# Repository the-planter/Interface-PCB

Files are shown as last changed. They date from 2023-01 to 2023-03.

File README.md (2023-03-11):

# Planter Interface PCB

Interface PCB for an automated hydroponics system, created using KiCad 6.0. 

This PCB enables control and interfacing a Raspberry with several liquid level sensors, 12V peristaltic pumps, a few temperature sensors, and remote controllable outlets.

This PCB acts as a carrier board for various off-the-shelf breakout boards. It enables noise-free signals, painless testing, and robust interfacing of the liquid level sensors, peristaltic pumps, air & water temperature sensors, and electrical outlets. Standardized connector types are used to guarantee secure connections; connector types are differentiated by their purpose and voltage level, to ensure no mismatch between components and voltage levels occur. The use of breakout boards alleviates the difficulties in procuring discrete Integrated Circuits (ICs) during the ongoing chip shortage. 

## Manufactured board
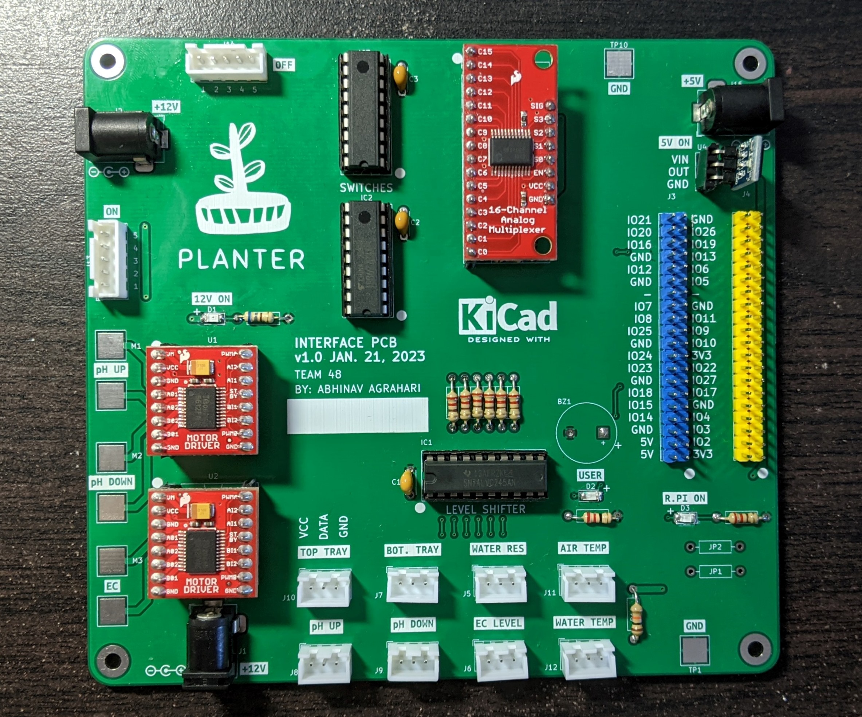
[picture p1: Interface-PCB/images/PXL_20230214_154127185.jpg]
Assembled PCB

| Left View | Right View |
| :---: | :---: |
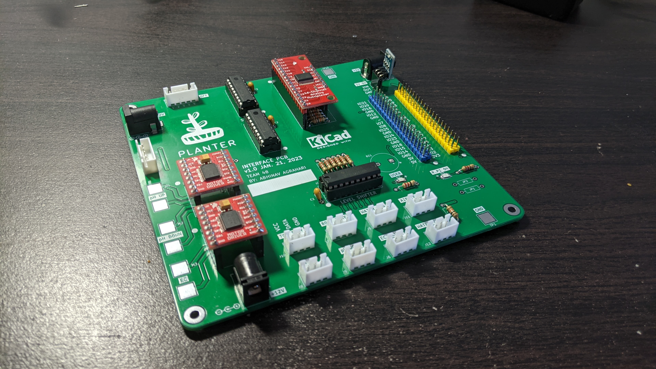
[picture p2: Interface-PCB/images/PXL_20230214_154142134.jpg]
Assembled PCB - Angled left
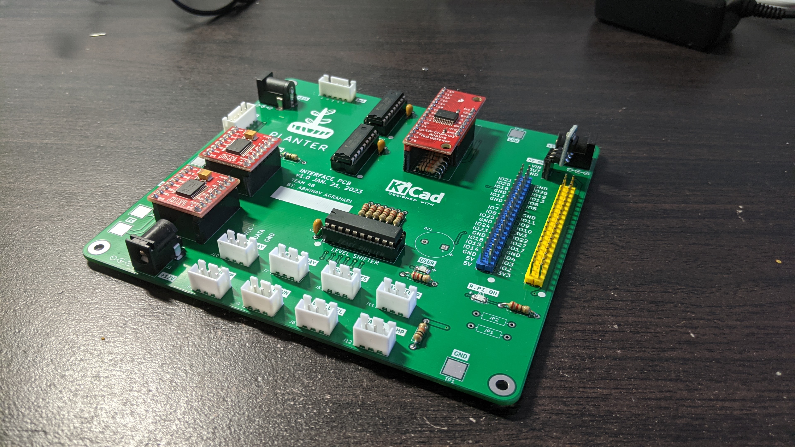
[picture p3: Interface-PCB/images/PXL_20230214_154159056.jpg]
Assembled PCB - Angled right
|  |  |

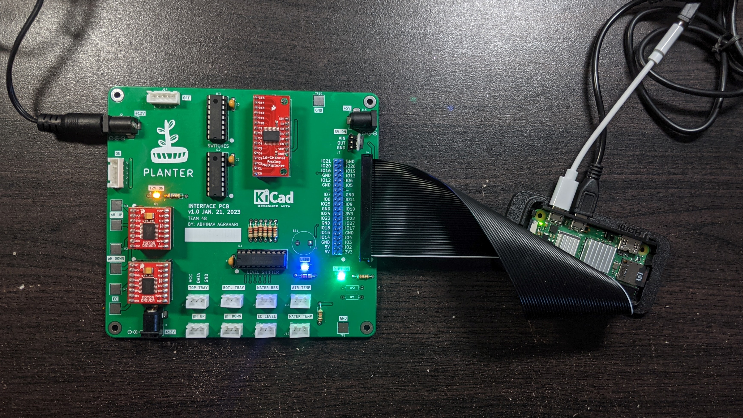
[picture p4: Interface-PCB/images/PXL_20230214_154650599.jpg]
PCB Blinky LED Test


Hooked up to all sensors:

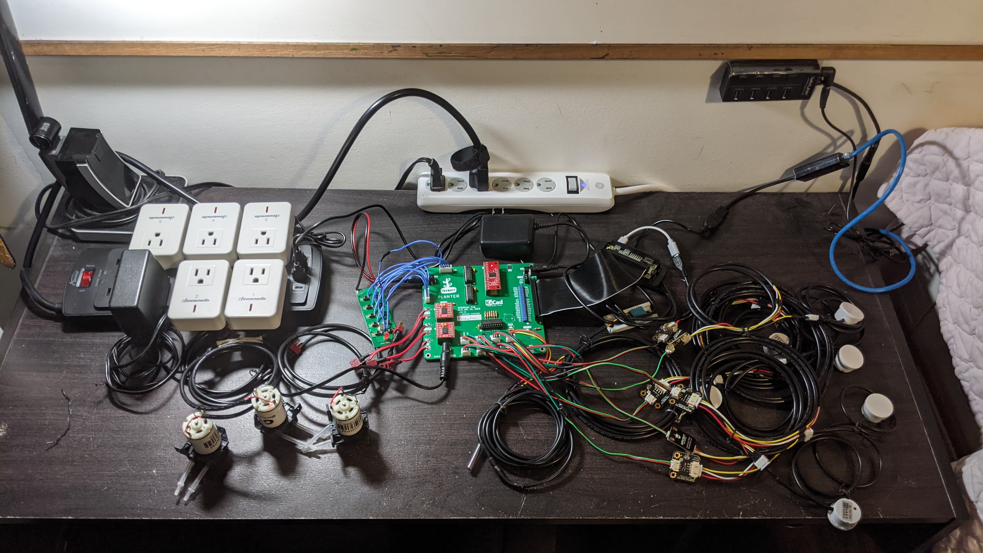
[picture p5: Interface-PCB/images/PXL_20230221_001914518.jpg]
All Electronics connected

## Renders
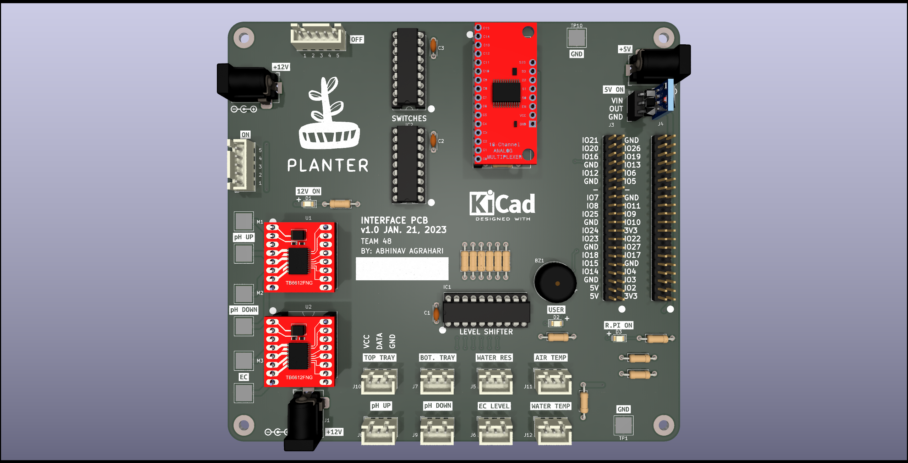
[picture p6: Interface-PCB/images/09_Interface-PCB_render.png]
PCB Render


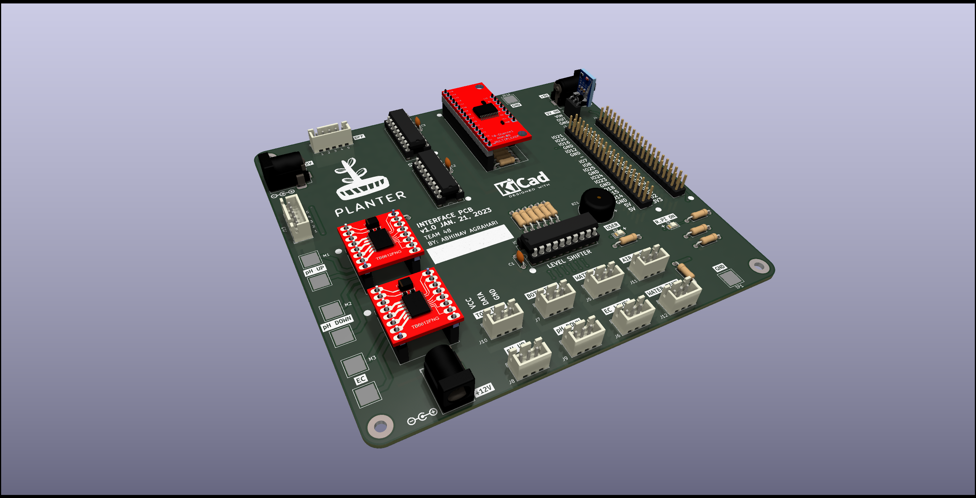
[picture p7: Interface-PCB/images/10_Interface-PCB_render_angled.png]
PCB Render angled

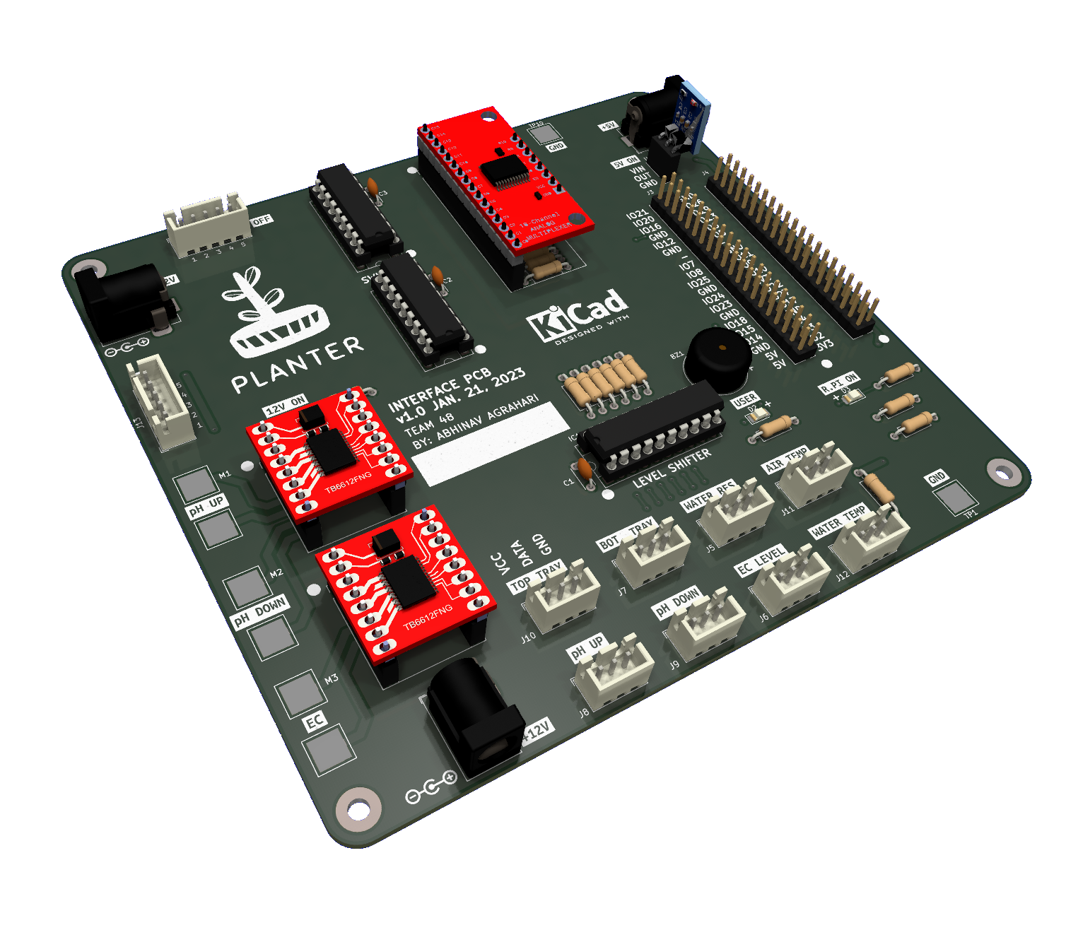
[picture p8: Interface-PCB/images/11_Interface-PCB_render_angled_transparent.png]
PCB Render angled


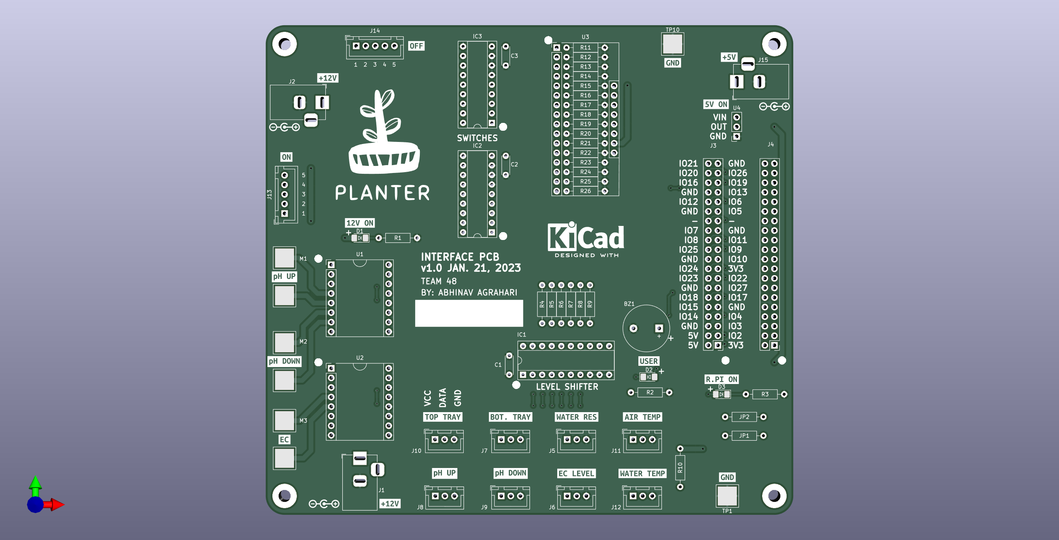
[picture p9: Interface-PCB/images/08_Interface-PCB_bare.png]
PCB Bare


## Routing
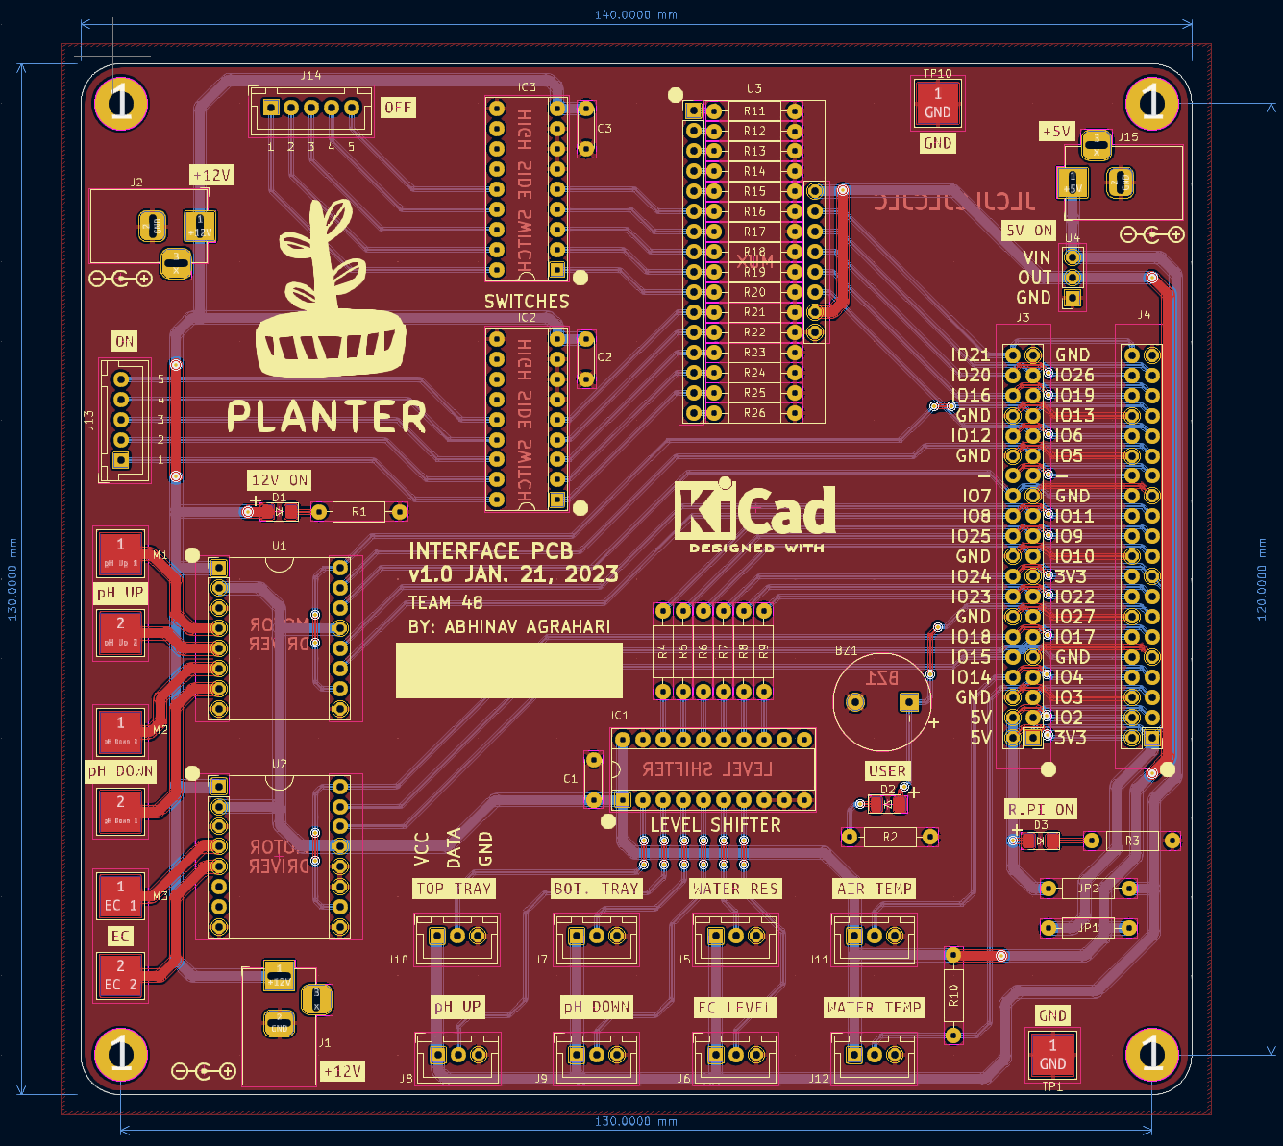
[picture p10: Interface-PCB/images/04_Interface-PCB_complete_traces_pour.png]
PCB Traces with Pour


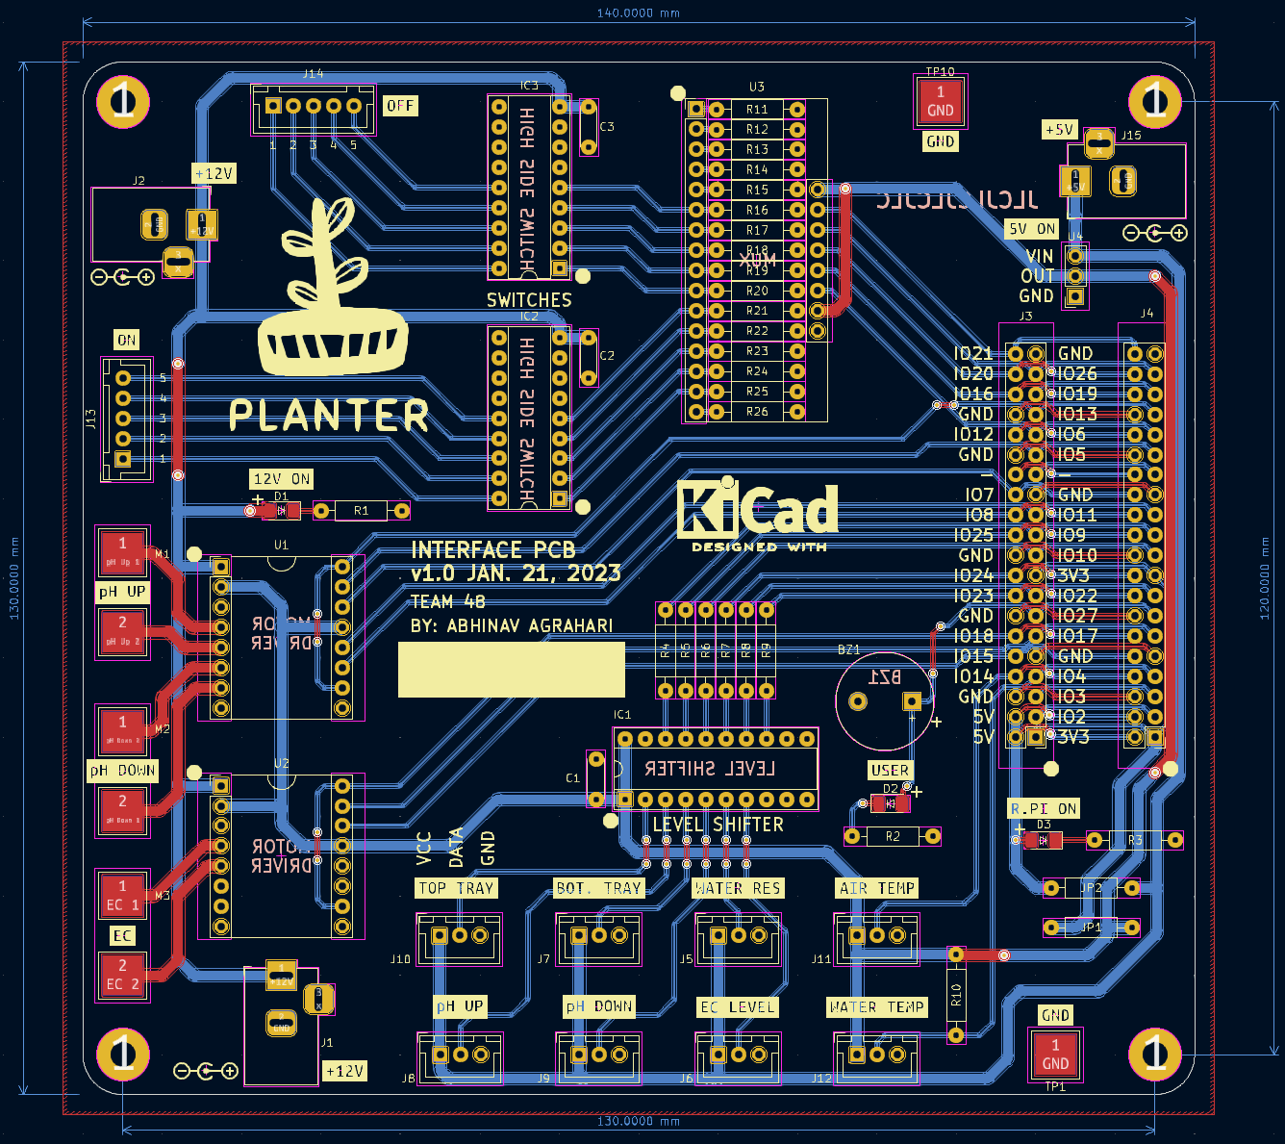
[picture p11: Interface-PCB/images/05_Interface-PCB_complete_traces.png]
PCB Traces


## Mechanical Team's Enclosure
The PCB is placed in the top shelf of the enclosure designed by the Mechanical Team
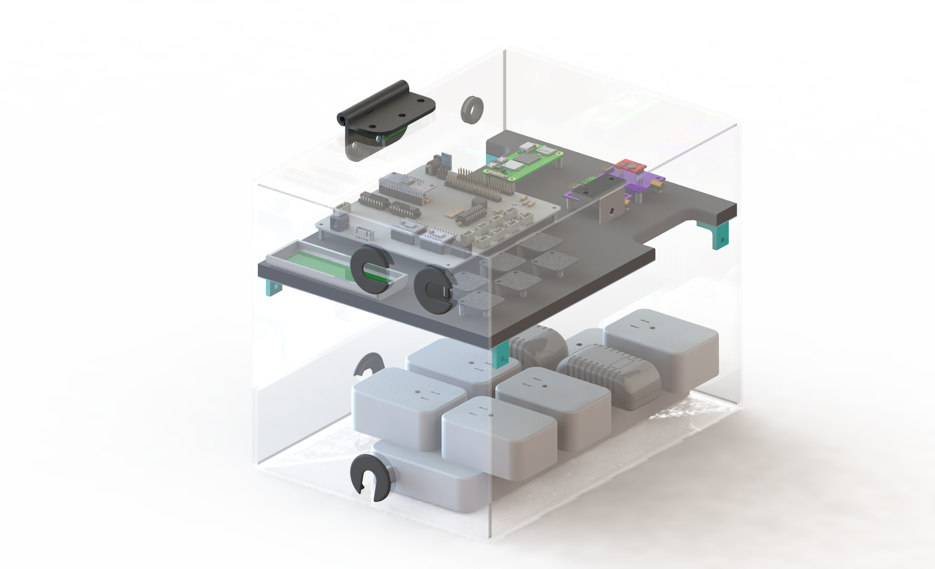
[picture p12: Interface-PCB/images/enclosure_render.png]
PCB in Enclosure - Rendered


## Schematic

Main Schematic
Sensors Schematic
Power Schematic
Remote Control Outlets Schematic

## Repo Setup
- Setup KiCad 6.0 using my [kicad-libraries](https://github.com/AbhinavA10/kicad-libraries)

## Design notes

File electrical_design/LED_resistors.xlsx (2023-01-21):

Purpose | Supply Voltage | LED Type | LED Color | FWD Voltage | FWD Current mA | FWD Current mA Designed | Calculated R Value | Closest 5% | Actual Current mA | R Power
Indicator | 12 | 3mm | RED | 1.85 | 20 | 15 | 676.6666667 | 680 | 14.9 | 0.1515036765
 | 12 | SMD | YELLOW | 1.8 | 20 | 15 | 680 | 680 | 15.0 | 0.153
Indicator | 5 | 3mm | GREEN | 2.1 | 20 | 15 | 193.3333333 | 220 | 13.2 | 0.03822727273
 | 5 | SMD | GREEN | 2.4 | 20 | 15 | 173.3333333 | 220 | 11.8 | 0.03072727273
User LED | 3.3 | 3mm | RED | 1.85 | 20 | 15 | 96.66666667 | 100 | 14.5 | 0.021025
 | 3.3 | SMD | BLUE | 3 | 20 | 15 | 20 | 22 | 13.6 | 0.004090909091

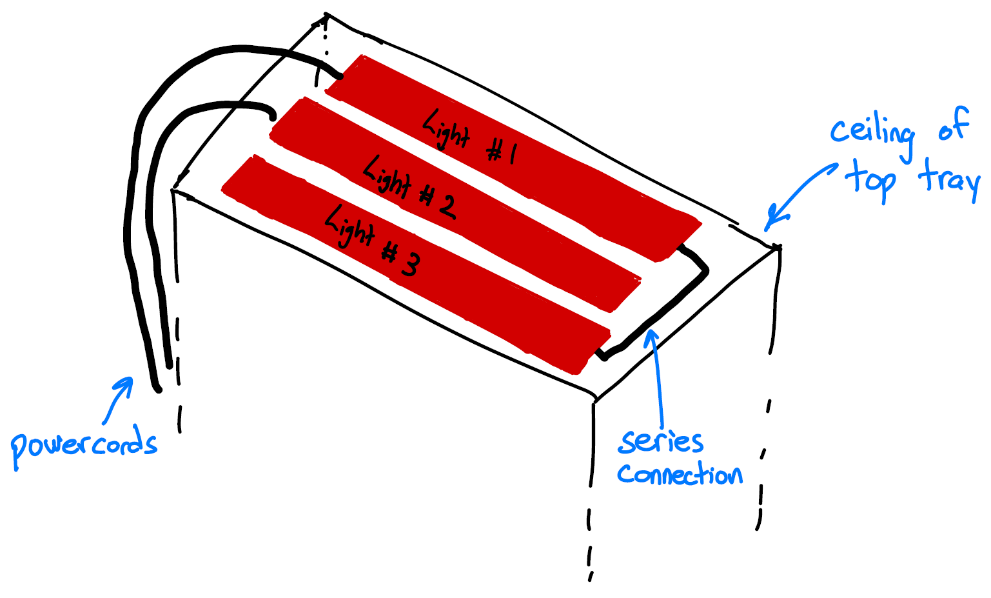
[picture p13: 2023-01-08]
electrical_design/Lights_position.png

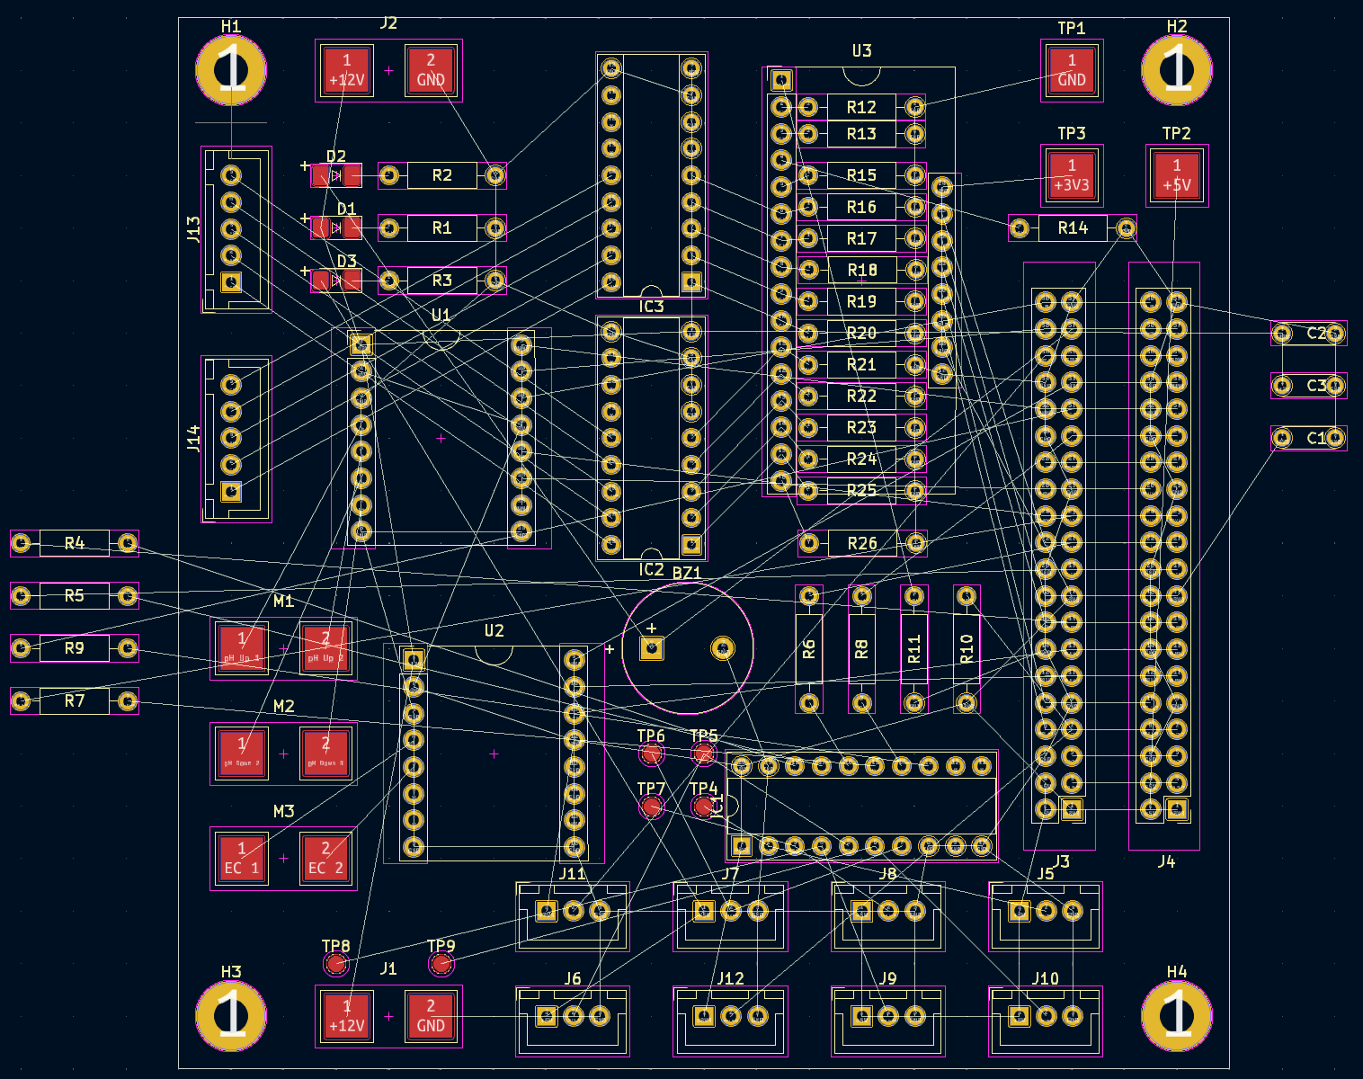
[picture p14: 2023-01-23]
Interface-PCB/images/00_initial_layout.png

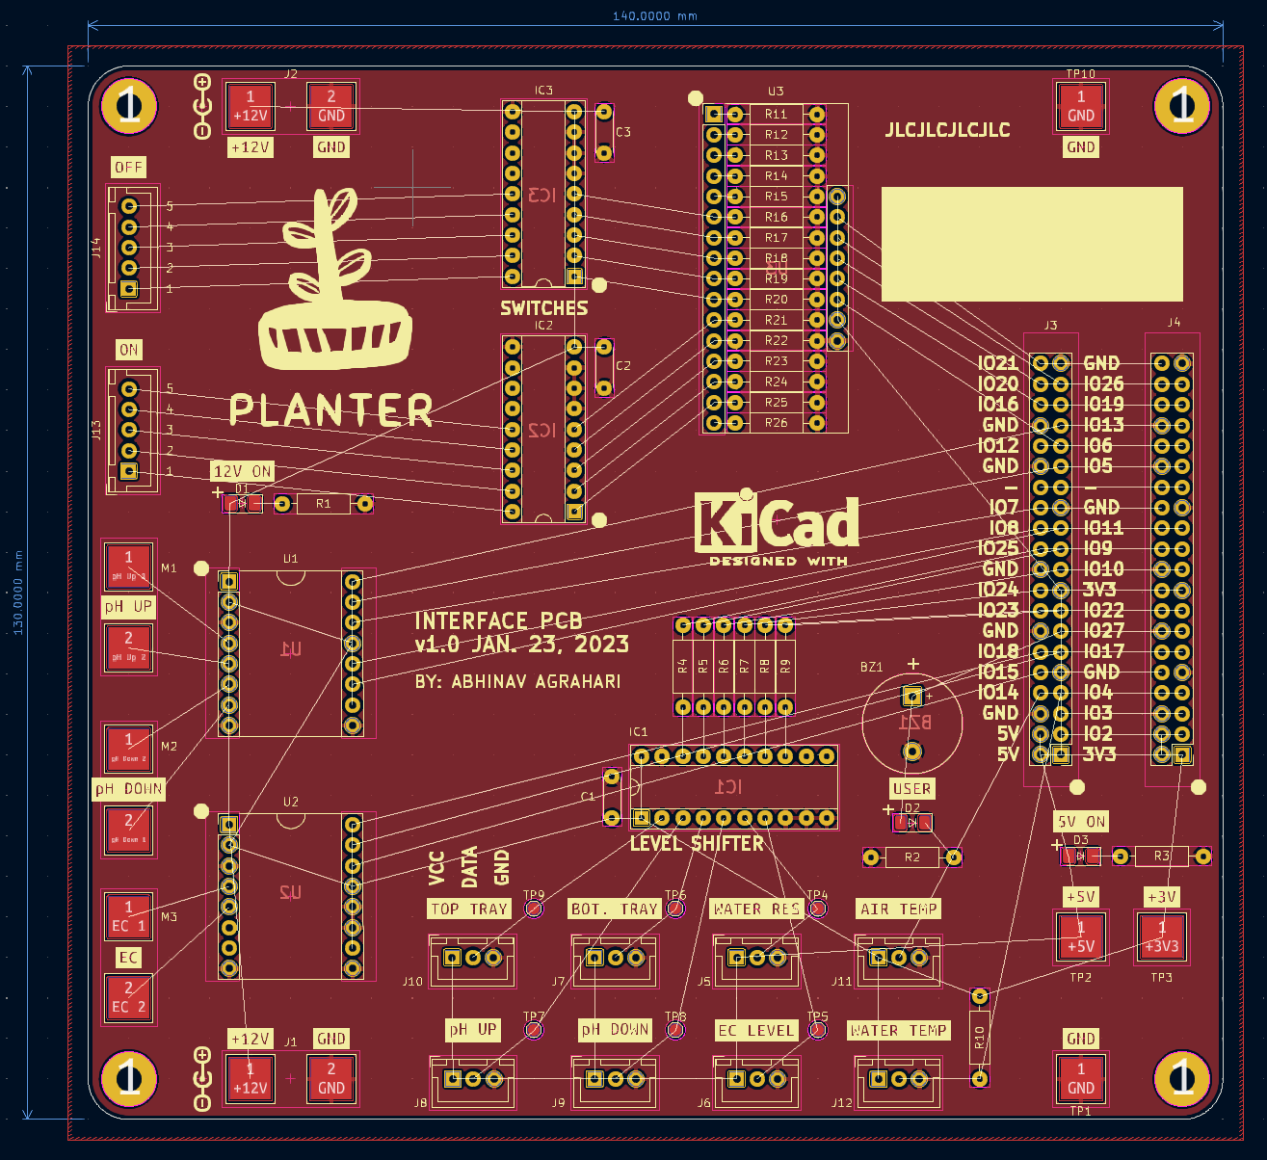
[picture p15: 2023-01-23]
Interface-PCB/images/03_complete_silkscreen.png

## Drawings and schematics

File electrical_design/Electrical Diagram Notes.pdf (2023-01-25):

PCBLayout | Custom PCB
/

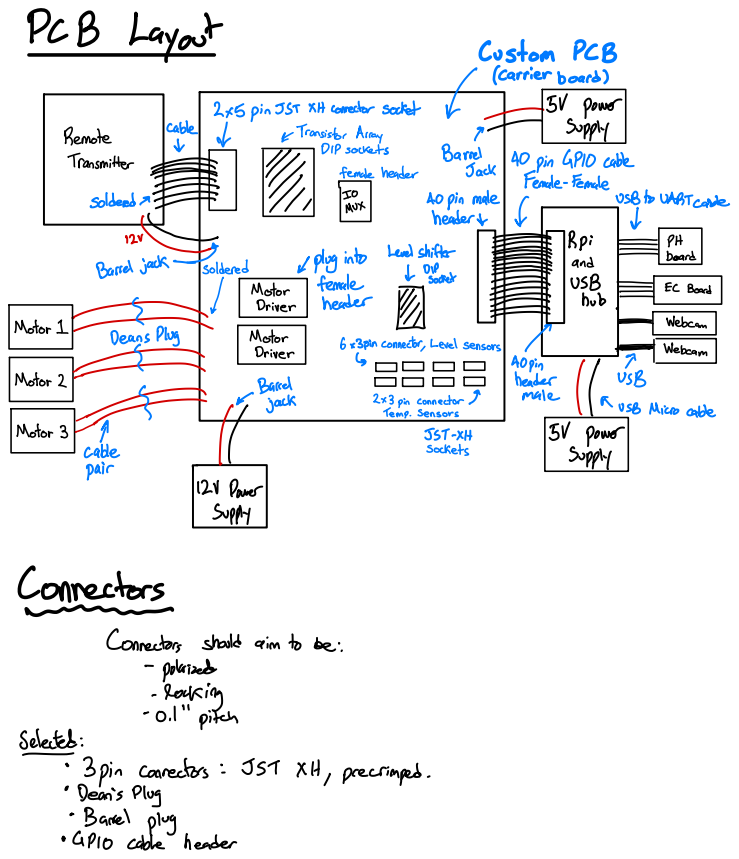
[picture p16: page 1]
(carrier board); 2x5 pin5STXHconnector socket; 50 power; Remote; cable; &Transistor Array; soppl; DIP sockets; Barrel Jack Transmitter -; ↑.'=x 40 pin GP10 cable ->; female header; Female-; Female; soldered a=; 40 pin male; USB toUARTble; header&; Rpi; PHd; Barrel jack &; soldered; Motor; female; ↓Plcket; Eand; Driver; header; nBb =; ICBoard; Motor I-; Webcam; Deans Plug; 6x3pinconnector, Level sensors; Iam; Motor 2; GOPe; Barrel; jack; 2x3 pin connector &; male; 1)aUSB Micro cable --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

↓ plug intoLevel shifter

Connectors should aim tobe:
polarized
·locking -
0.1"pitch

selected3pin connectors:JST XH, precrimped ·

# Baboard Dimensions Pitch -

90.1"

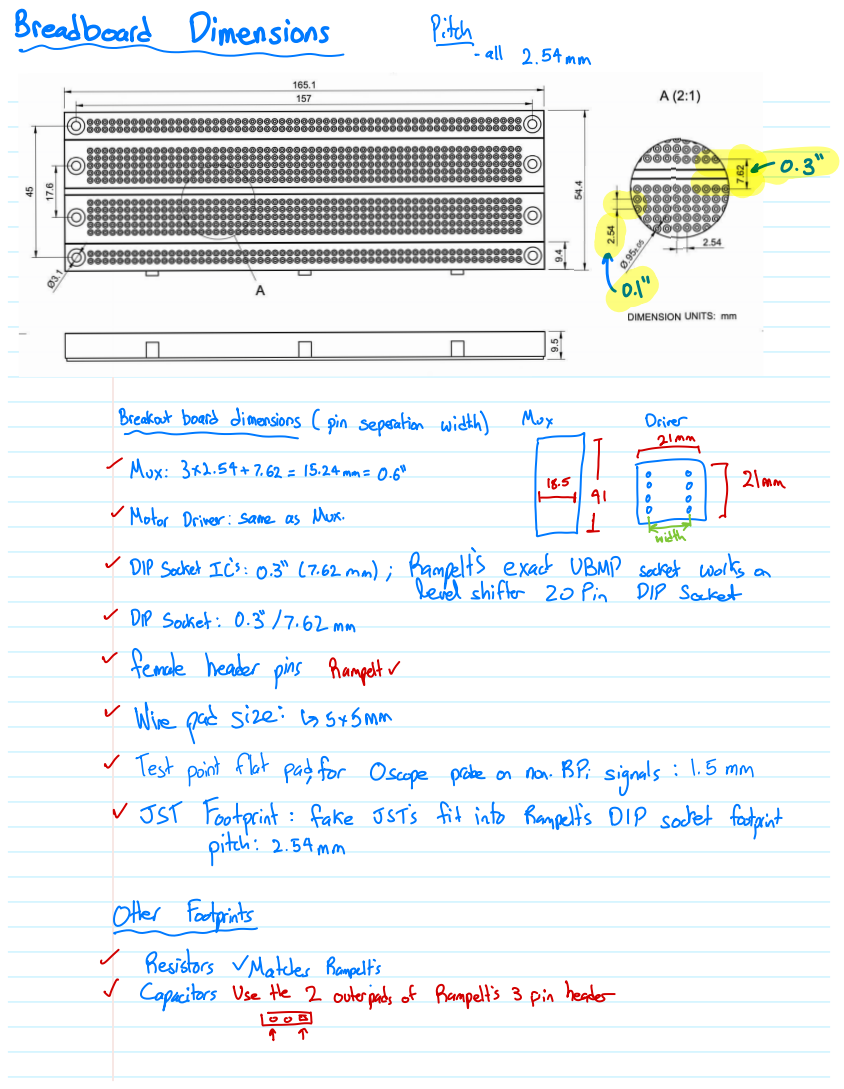
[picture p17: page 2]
all 2.54mm; Breakoutboard dimensions -; (pin separation width); Mox; Driver; Mox:3x2.54+ 7.62 =; Day7:JCl; ~Motor Driversame as; Nux.; kith!; level shifter 20 Pic; DIP socket; ~ Testpointflatpad, for Oscope probe on; non. RPisignals:¹.5 mm; #Footprints; Resistors ~Matches Rampelt's

~ DIP SocketICs:0.3" (.62mm);Rampelt's exactUBMPsocret works or

~ DIPSocket:0.3" /7.62mm
female header pins Rampeltr

~ Wire pad size:25x5mm
~JSTFootprint: fake JST's fitinto Rampelt's DIPsocket footprint
pitch: 2.54mm

v Capacitors Use the 2 outerpads ofRampelt's 3 pin header

# For

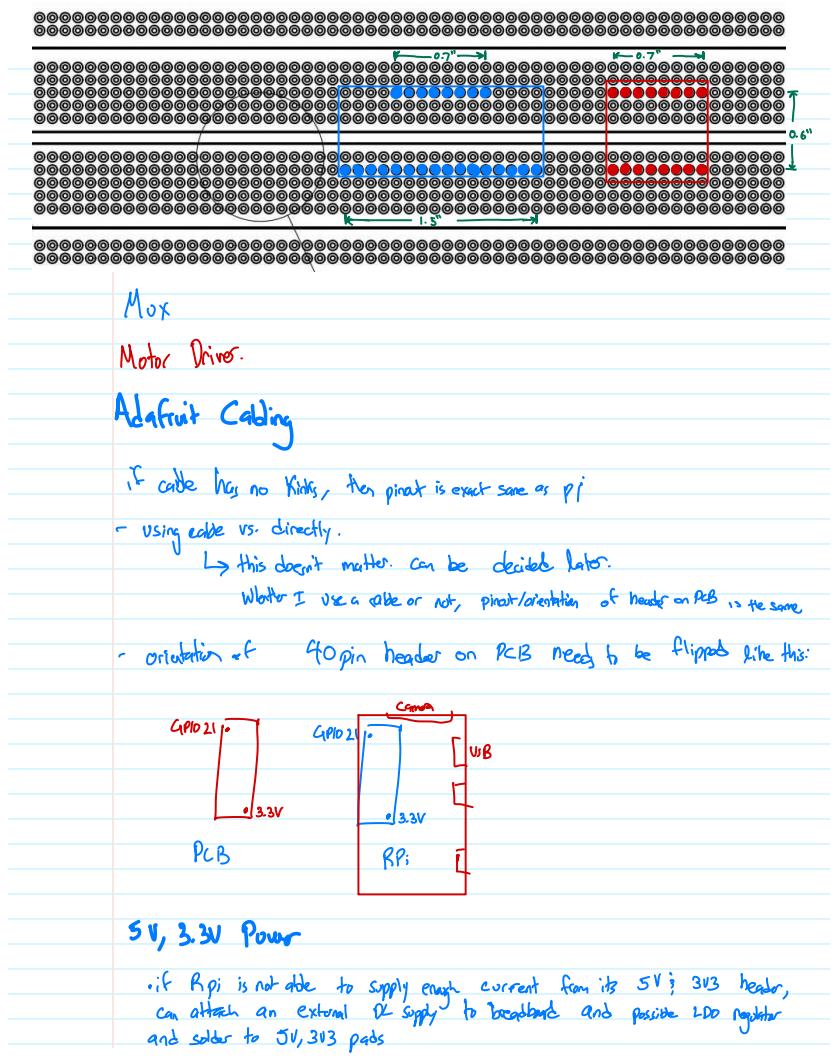
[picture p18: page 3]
Mox; Motor Driver. AdafruitCabling; ifcable has no; kinks, the pinoutis exactsame as; using eable vs. directly.; ↳ this doesn'tmatter. can be; decided later.; Whatter I use a cable or; not, pinotorientation ofheader on PCB is the same; orientation of40pin header on; PCB needs to be; flipped like this:; carea; PCB; can attach an; external; DC supplyto "breadboard and possible CDO regulator and solder to 50,303 pads

5V, 3.30 Power
· ifRpiis notable to supplyenough currentfrom its5V;,303 header,

# Rough BlockDiagrams. Initial Planning

10 NPN transisters | -> | VART

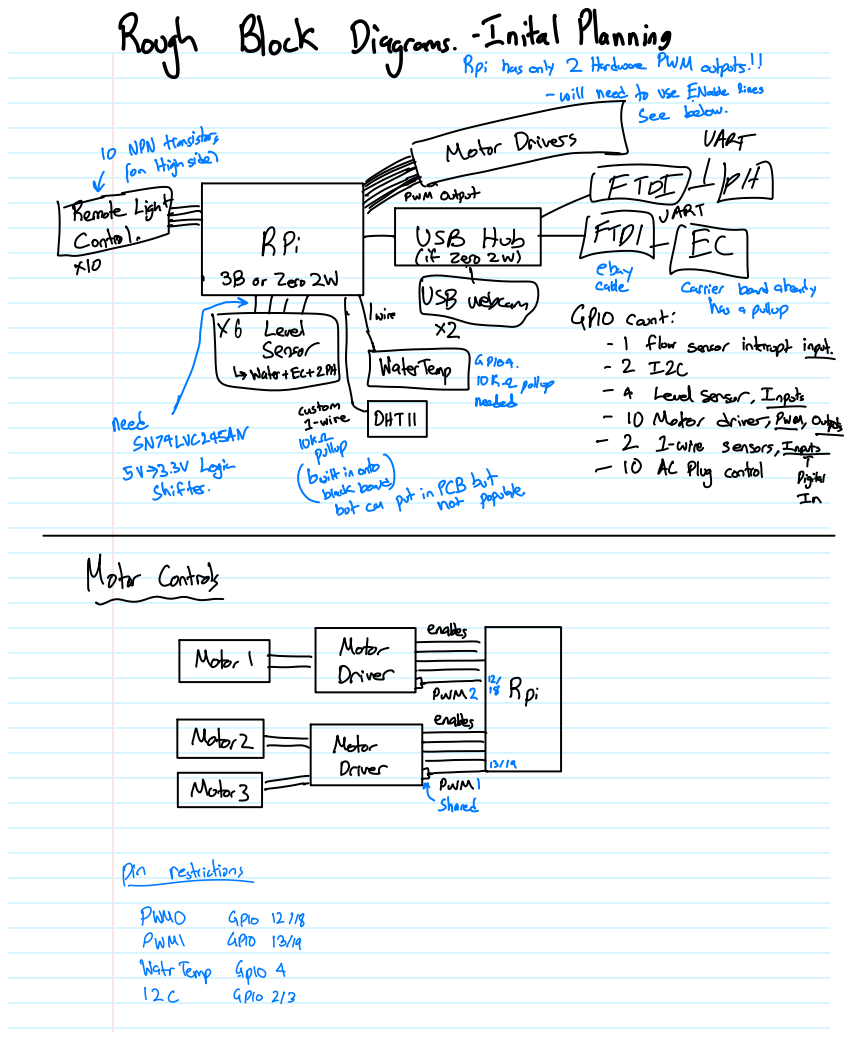
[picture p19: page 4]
see below.; 100 High side); #-puM output; noteLight; ENTERTA; VART; RPi; USB Hub; 3Bor Zero2W; ebay; cable; carrier board already; count:; has a pullup; flow sensor; interruptit. ↑ ⑭ter Tempa P164.; 10kpollo; needed; lead sensor, Inpots; needNT4LVC245AN customre; PHT 1; 10 Motor driver, Iran, opts; 2 I-wire; sensors,Inputs pullup; 5V93.3V Logic; Iwiltin onto&; 10 AC Plug control; Digital shifter.; L blackboard; putinPCB boopulate.; butcal; ↑Controls; enables; MotoI; Motor⁻; PNM2; BRpi; nables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

Rpihas only2 Hardware PWM outpots!!
x2 #sectio reson ano

will need touse Nable lines

Remote Control torequirementsfrom testing.

## 44mAon button

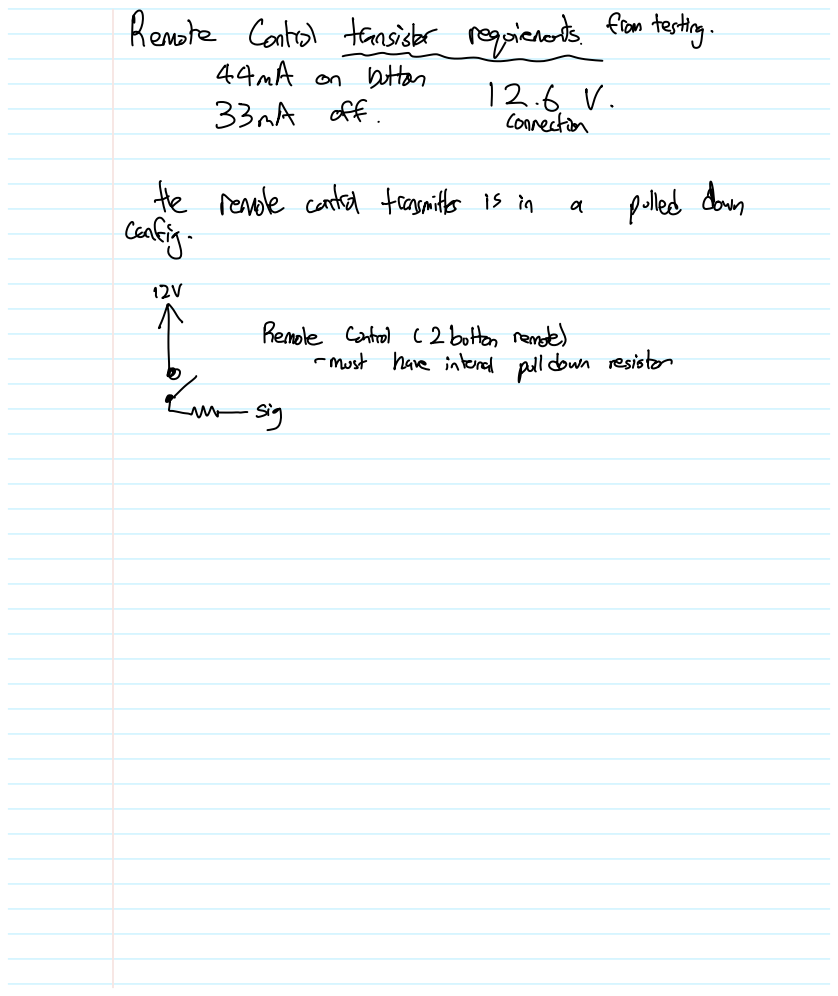
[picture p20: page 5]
33mAoff.; connection; the remote control transmitter is in; polled down; config.; ! Remote Control; (2button remote)

musthave internal pull down resistor
sig

# Routine Blockage norigged

# clogged

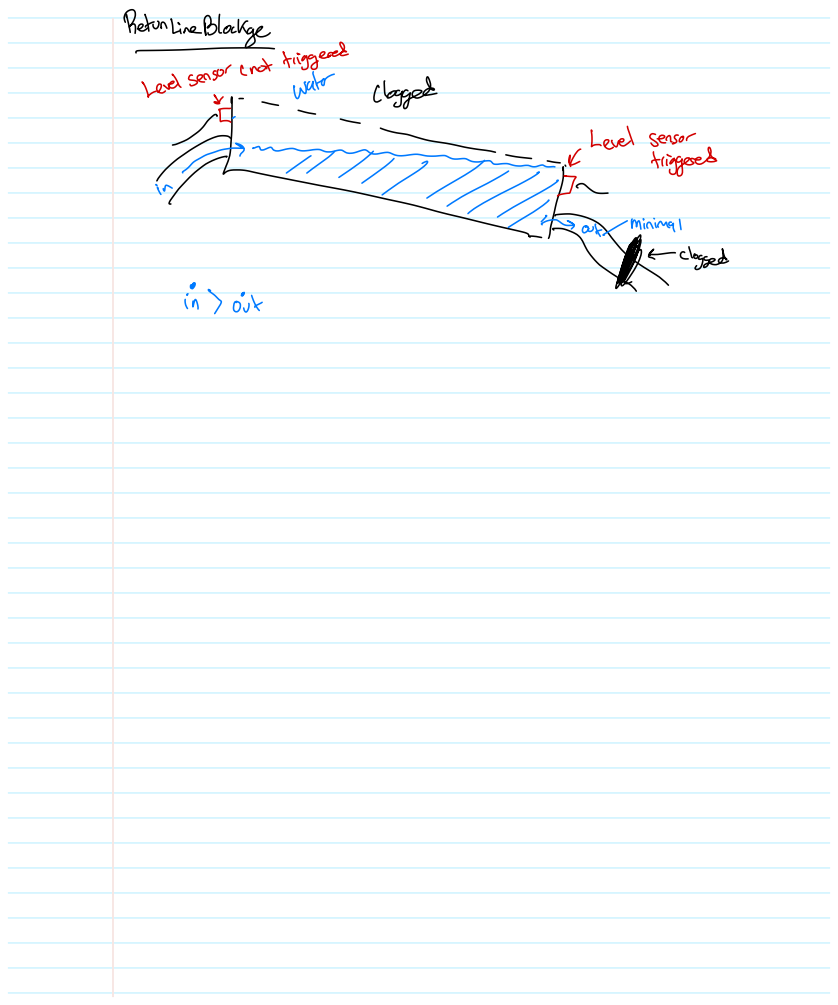
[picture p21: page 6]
Level sensor; triggered i; clogged

# Top

## try

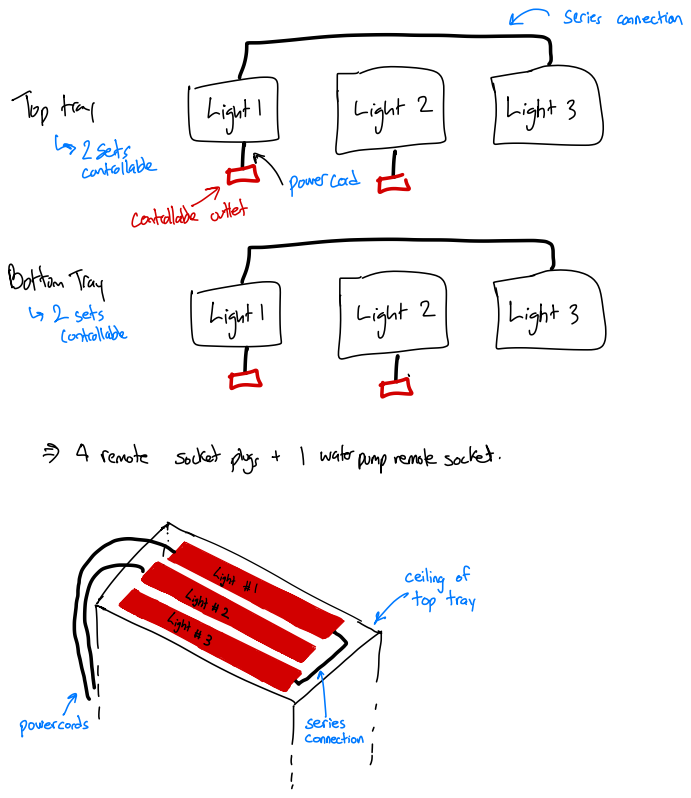
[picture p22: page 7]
& series connection; Isets; ⑭nights; controllable; powercod ↓; controllablertet; Bottom Tray; ⑭its ↳ 2 sets; => I remotesocketplugs + 1 water; top to; * alis &; powercords

pump remote socket.

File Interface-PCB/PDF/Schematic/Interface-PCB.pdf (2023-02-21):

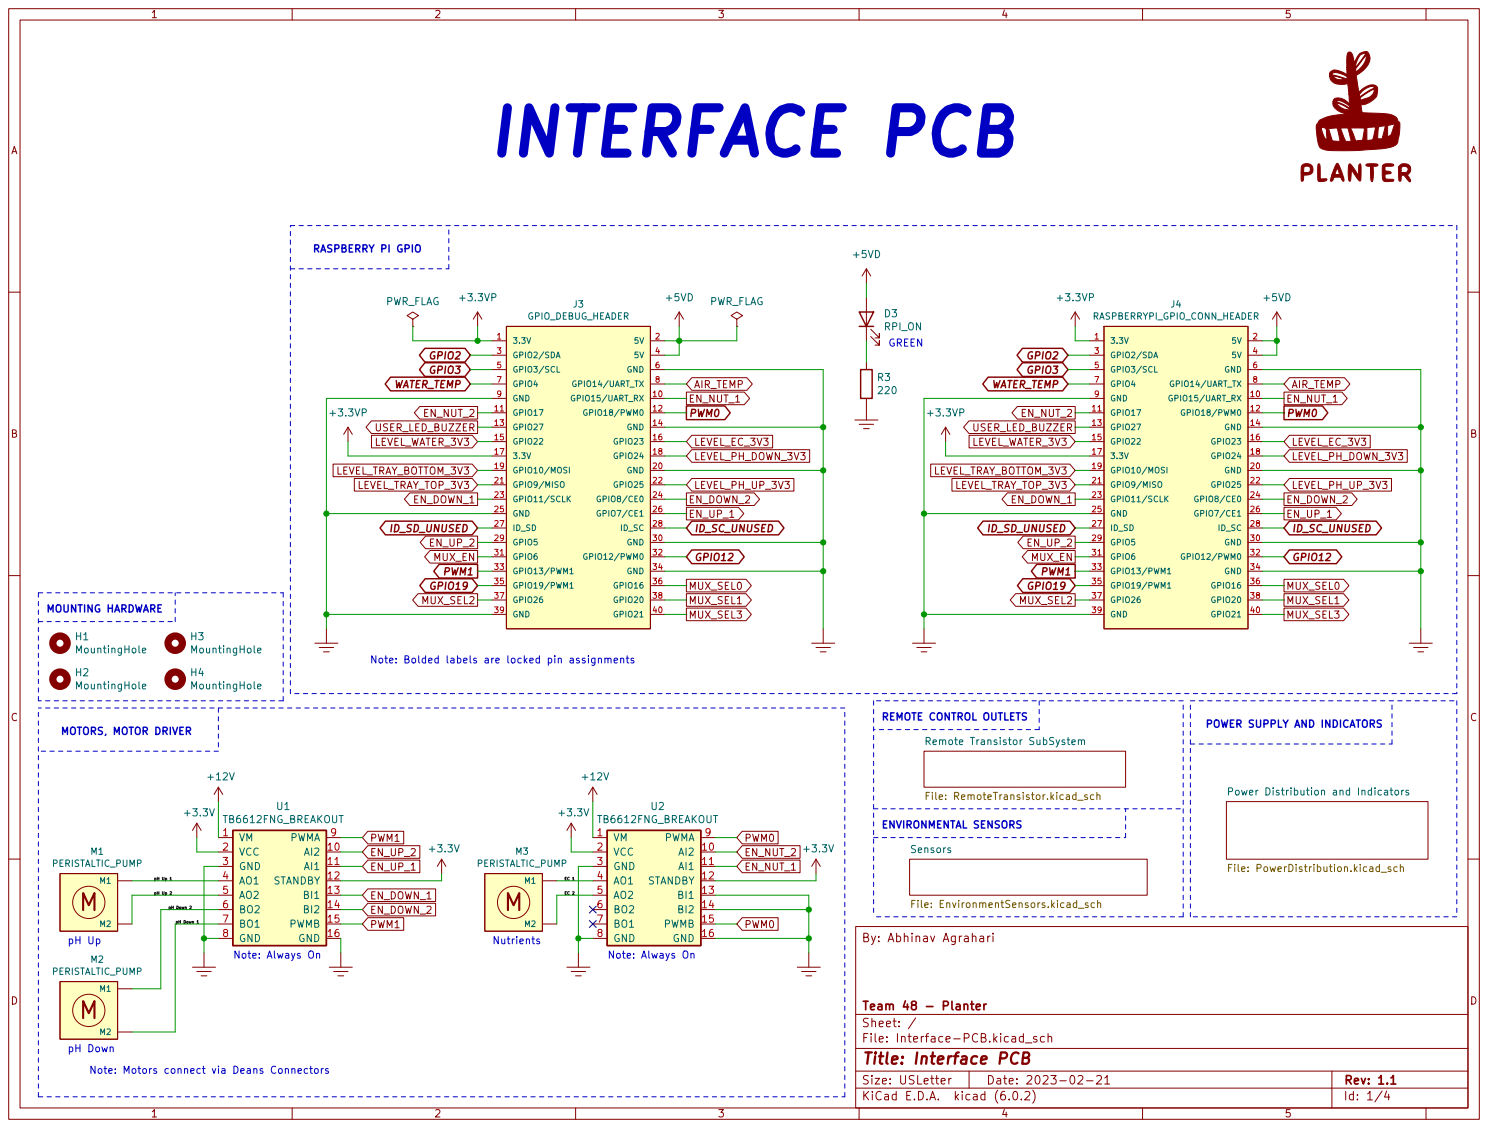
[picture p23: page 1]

GREEN MOTORS, MOTOR DRIVER

pH Down 2

File: Interface-PCB.kicad_sch Sheet: / Team 48 - Planter By: Abhinav Agrahari

Id: 1/4 Title: Interface PCB

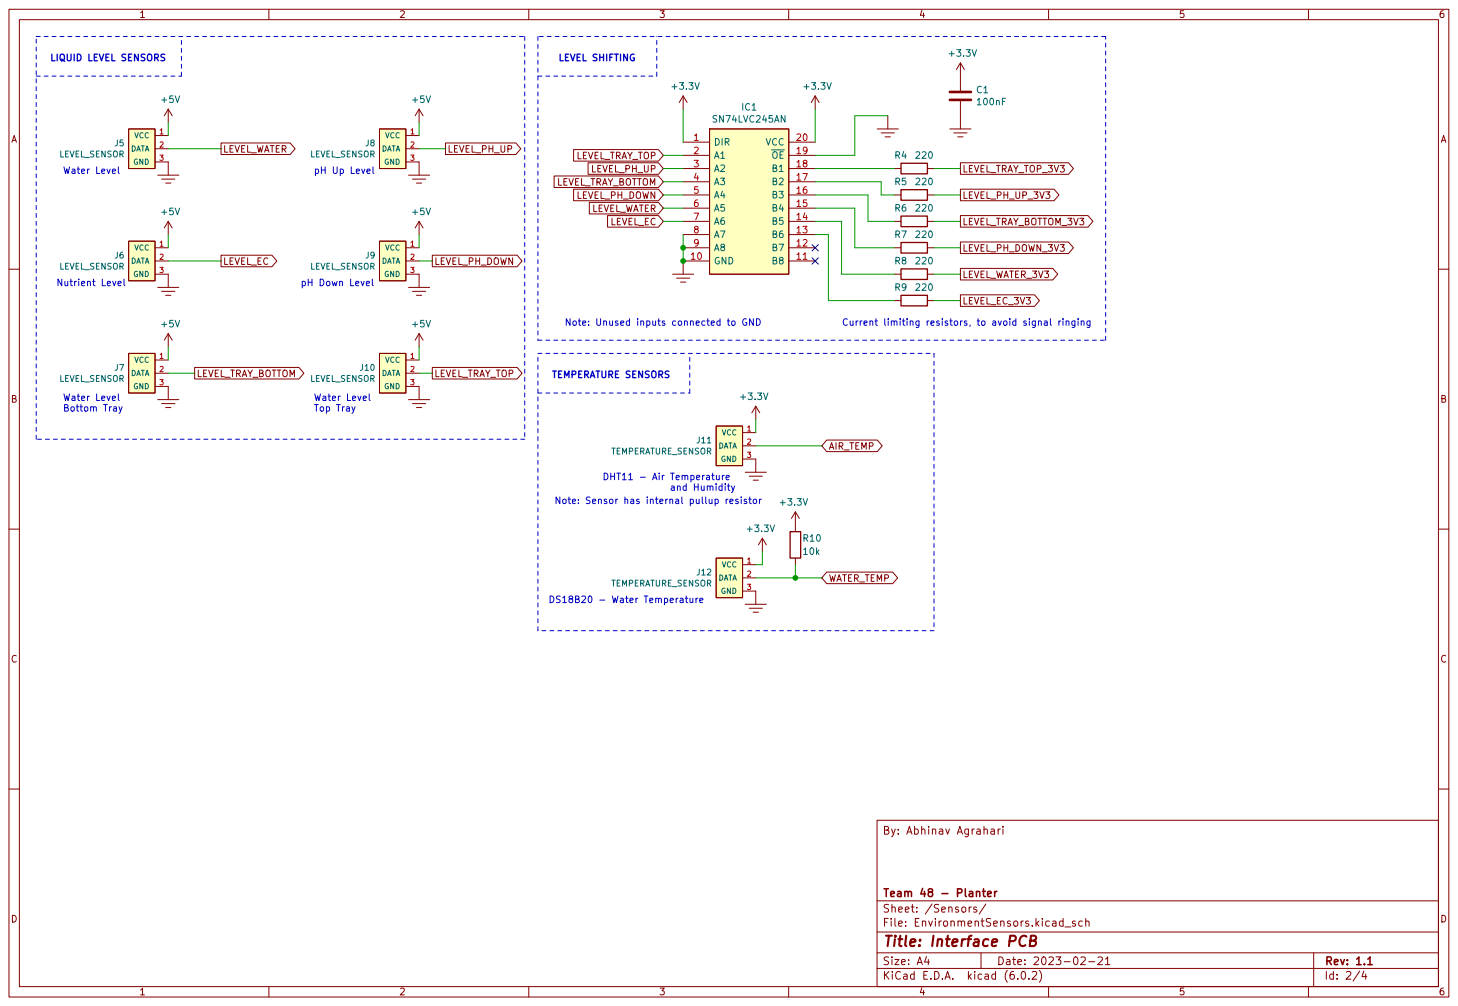
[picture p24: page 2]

pH Up Level LIQUID LEVEL SENSORS Nutrient Level Water Level Bottom Tray

Note: Sensor has internal pullup resistor

Id: 2/4 Title: Interface PCB

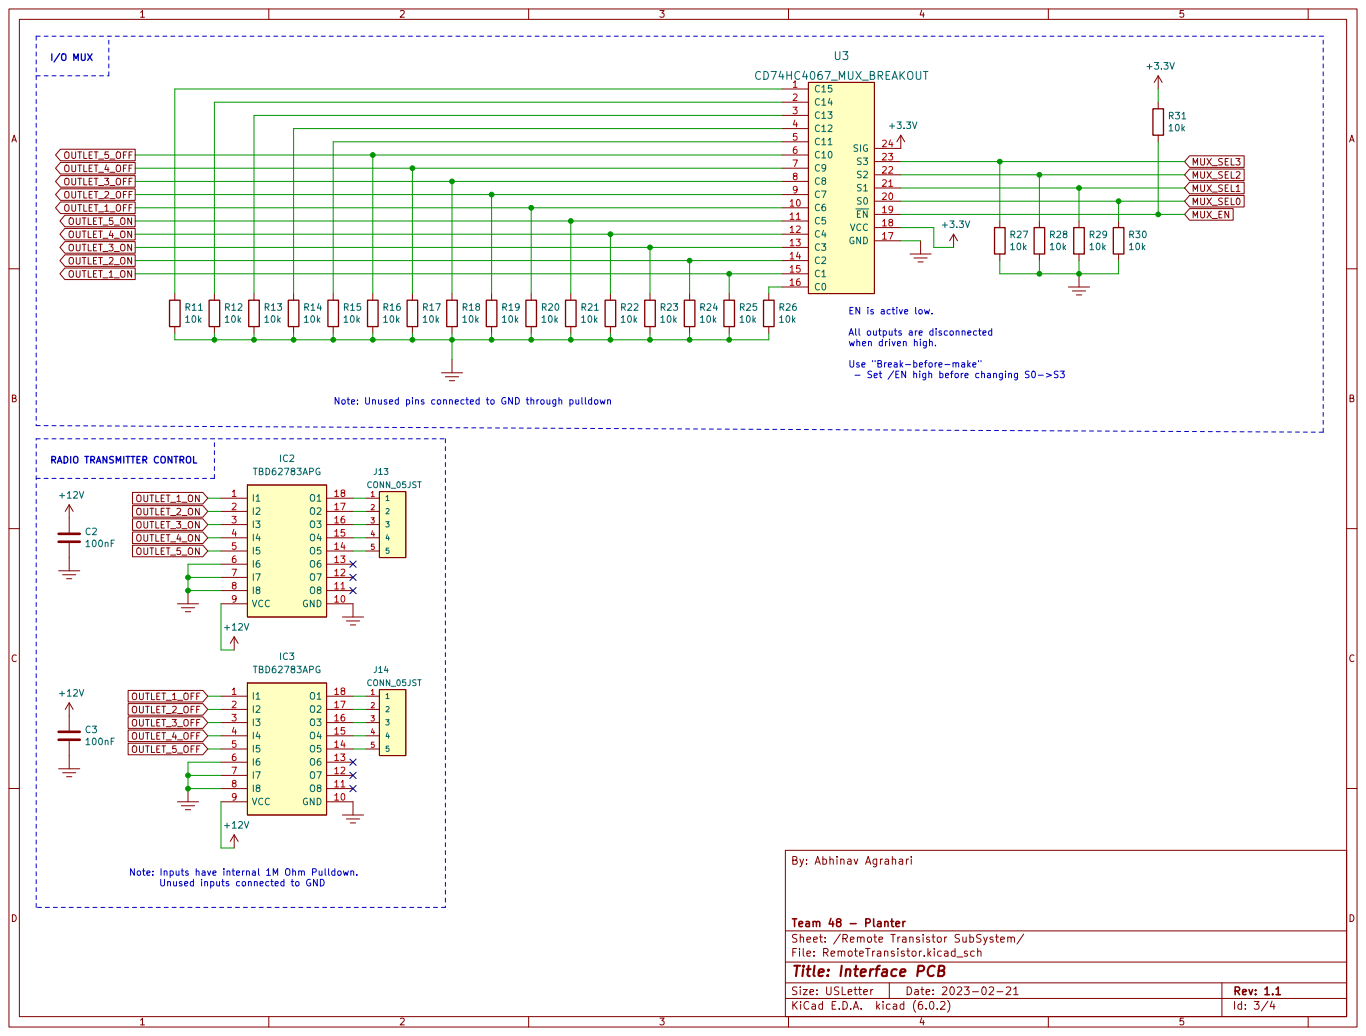
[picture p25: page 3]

EN is active low. All outputs are disconnected

when driven high. Use "Break-before-make"

- Set /EN high before changing S0->S3

Note: Unused pins connected to GND through pulldown

I2 2 | 2
I3 3 | 3
I4 4 | 4

Sheet: /Remote Transistor SubSystem/ Team 48 - Planter By: Abhinav Agrahari

Note: Inputs have internal 1M Ohm Pulldown.
Unused inputs connected to GND

File: RemoteTransistor.kicad_sch
Id: 3/4 Title: Interface PCB

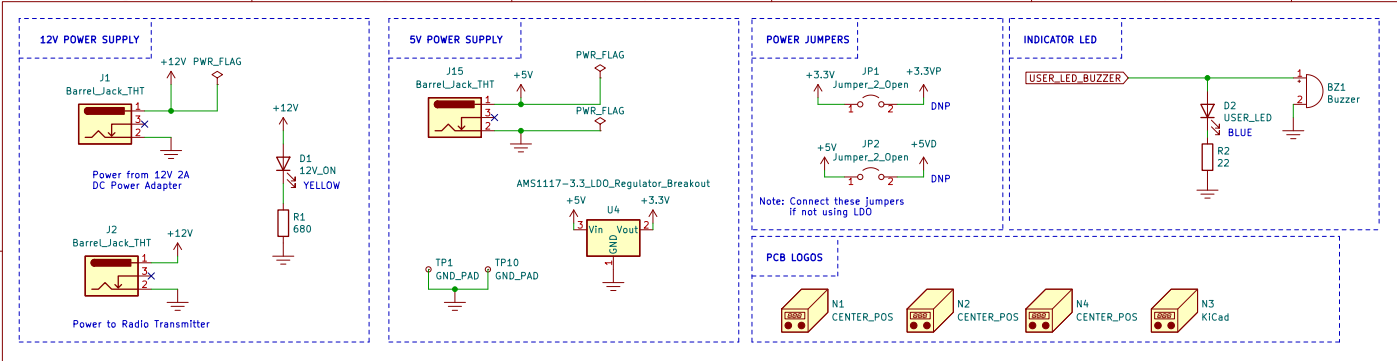
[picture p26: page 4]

Power from 12V 2A DC Power Adapter

Note: Connect these jumpers
if not using LDO

File: PowerDistribution.kicad_sch Sheet: /Power Distribution and Indicators/ Team 48 - Planter By: Abhinav Agrahari

Id: 4/4 Title: Interface PCB

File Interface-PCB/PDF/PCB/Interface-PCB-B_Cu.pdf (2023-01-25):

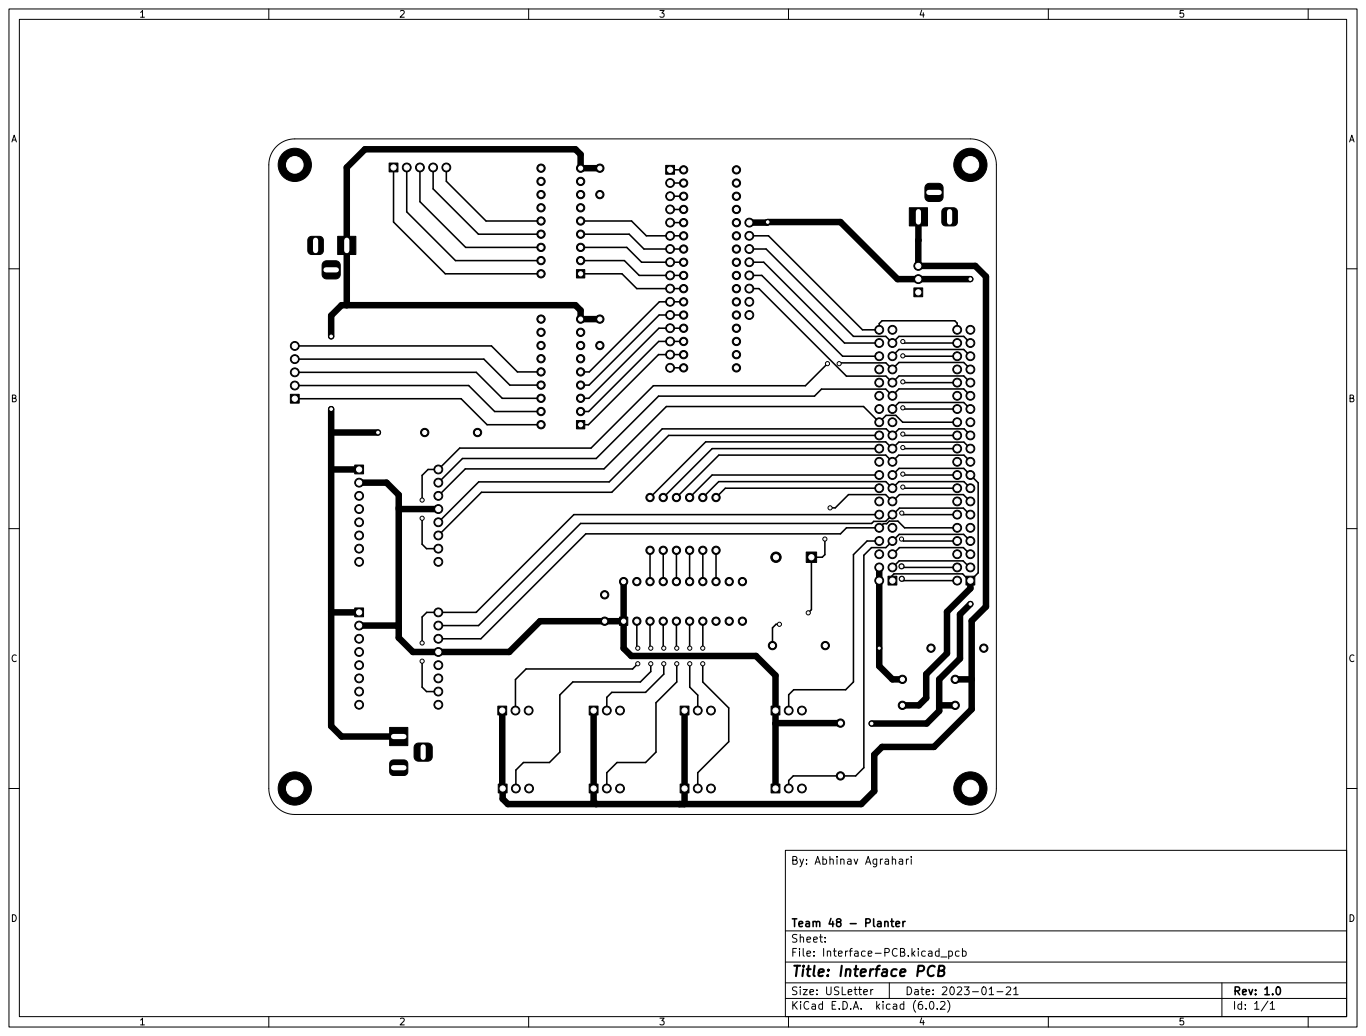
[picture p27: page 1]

File: Interface-PCB.kicad_pcb Sheet: Team 48 - Planter By: Abhinav Agrahari

Id: 1/1 Title: Interface PCB

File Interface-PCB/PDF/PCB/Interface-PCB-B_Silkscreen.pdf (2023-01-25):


Id: 1/1 Title: Interface PCB

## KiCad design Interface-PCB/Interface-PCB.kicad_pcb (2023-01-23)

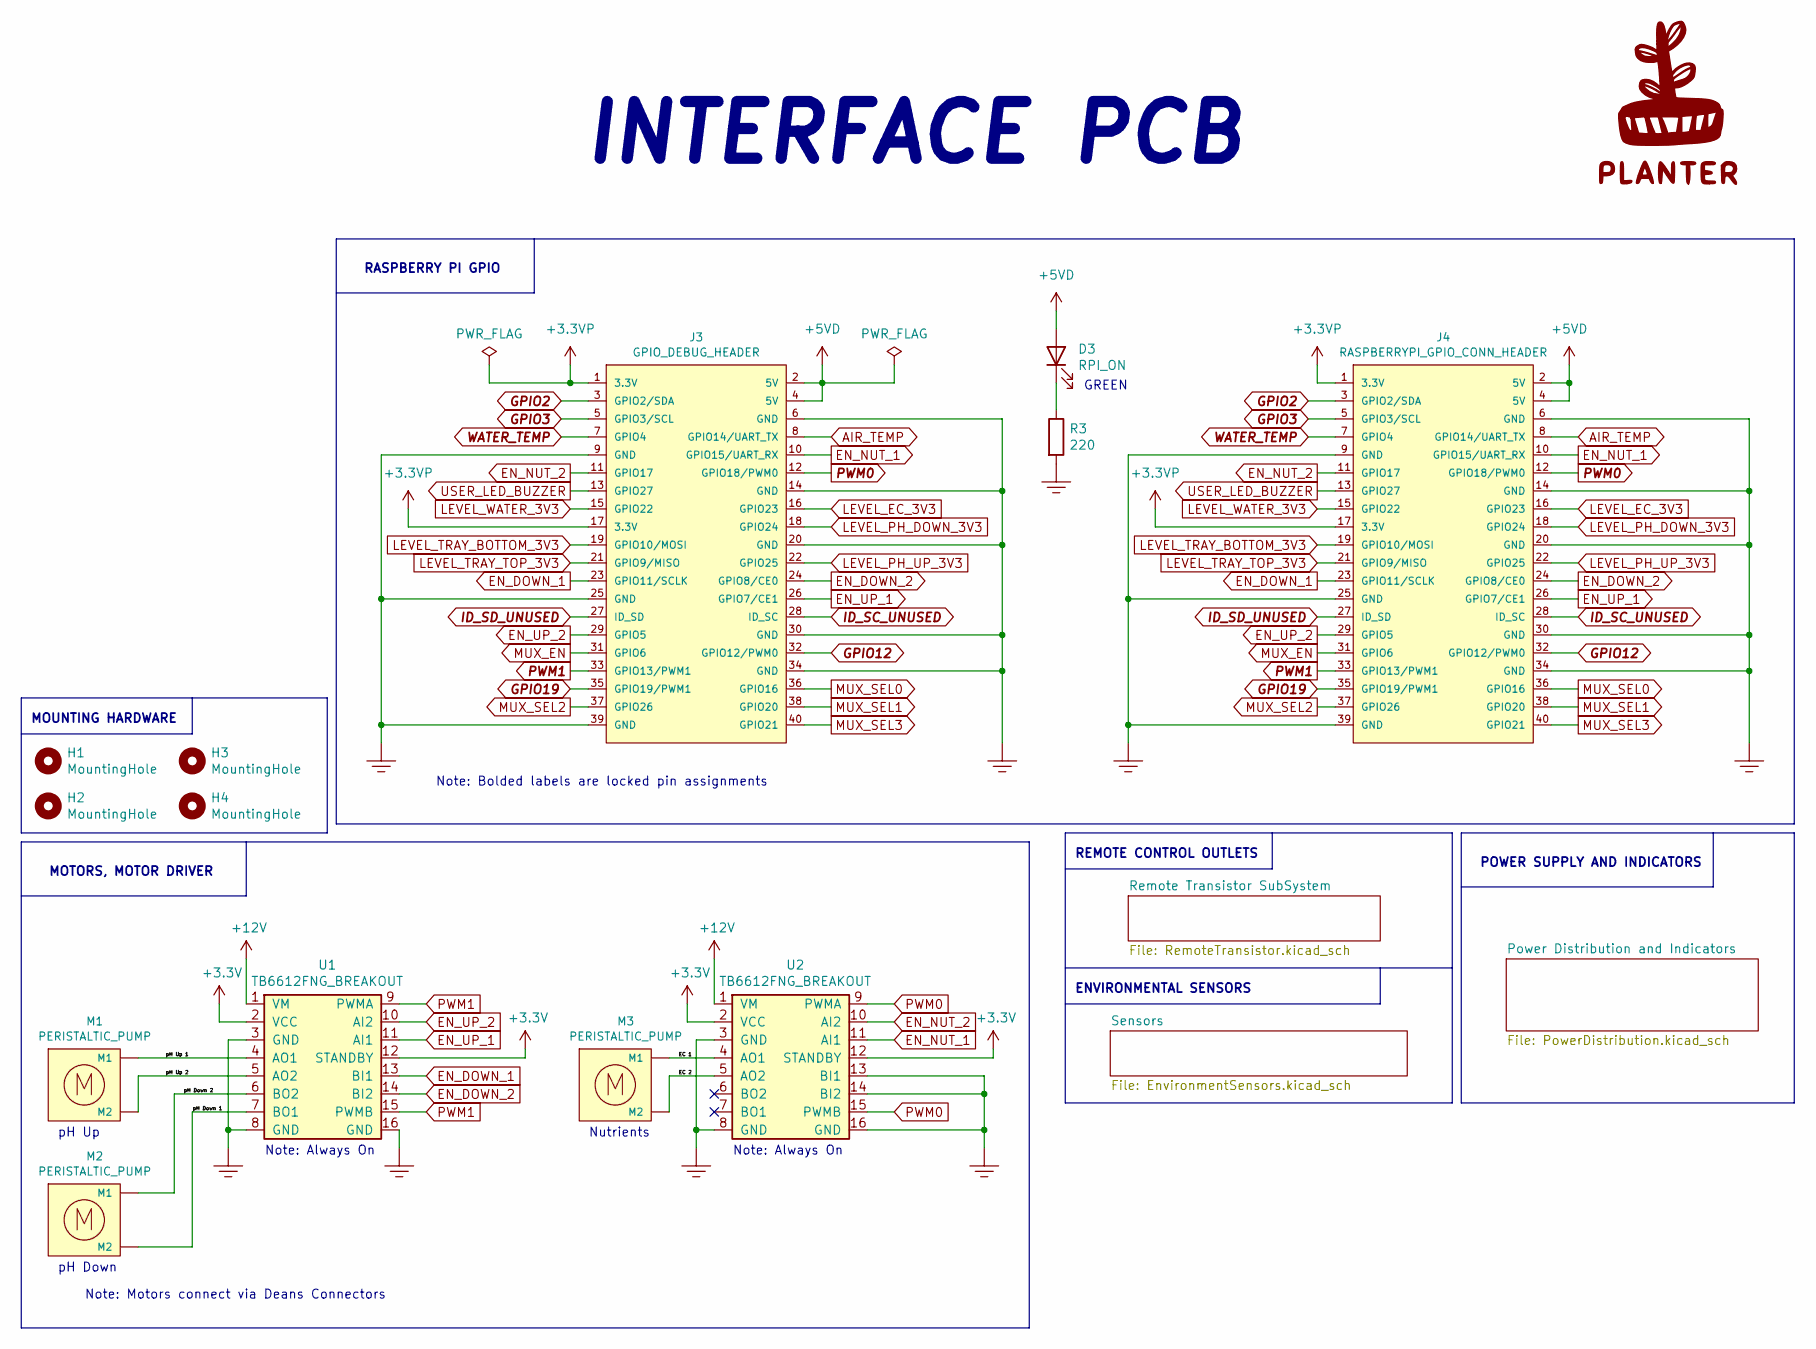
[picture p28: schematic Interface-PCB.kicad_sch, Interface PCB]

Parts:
D3: RPI_ON; LED_SS_1206_3216Metric_Pad1.42x1.75mm_HandSolder
G1: PLANTER_LOGO_8mm; PLANTER_LOGO_30MM_SILKSCREEN
H1, H2, H3, H4: MountingHole; MountingHole_3.2mm_M3_Pad
J3: GPIO_DEBUG_HEADER; RASPBERRYPI-40-PIN-GPIO-2x20_P2.54mm_Vertical
J4: RASPBERRYPI_GPIO_CONN_HEADER; RASPBERRYPI-40-PIN-GPIO-2x20_P2.54mm_Vertical
M1, M2, M3: PERISTALTIC_PUMP; PowerPad_Pair_5.0x5.0mm
R3: 220; R_SS_Axial_DIN0207_L6.3mm_D2.5mm_P10.16mm_Horizontal
U1, U2: TB6612FNG_BREAKOUT; TB6612FNG_Breakout; Digikey_Part_Number 1568-1755-ND

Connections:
+3.3VP: J3.1 (3.3V), J3.17 (3.3V), J4.1 (3.3V), J4.17 (3.3V); also elsewhere on the board
+3V3: U1.2 (VCC), U1.12 (STANDBY), U2.2 (VCC), U2.12 (STANDBY); also elsewhere on the board
+5VD: D3.2 (A), J3.2 (5V), J3.4 (5V), J4.2 (5V), J4.4 (5V); also elsewhere on the board
+12V: U1.1 (VM), U2.1 (VM); also elsewhere on the board
/EC 1: M3.1 (M1), U2.4 (AO1)
/EC 2: M3.2 (M2), U2.5 (AO2)
/pH Down 1: M2.2 (M2), U1.7 (BO1)
/pH Down 2: M2.1 (M1), U1.6 (BO2)
/pH Up 1: M1.1 (M1), U1.4 (AO1)
/pH Up 2: M1.2 (M2), U1.5 (AO2)
AIR_TEMP: J3.8 (GPIO14/UART_TX), J4.8 (GPIO14/UART_TX); also elsewhere on the board
EN_DOWN_1: J3.23 (GPIO11/SCLK), J4.23 (GPIO11/SCLK), U1.13 (BI1)
EN_DOWN_2: J3.24 (GPIO8/CE0), J4.24 (GPIO8/CE0), U1.14 (BI2)
EN_NUT_1: J3.10 (GPIO15/UART_RX), J4.10 (GPIO15/UART_RX), U2.11 (AI1)
EN_NUT_2: J3.11 (GPIO17), J4.11 (GPIO17), U2.10 (AI2)
EN_UP_1: J3.26 (GPIO7/CE1), J4.26 (GPIO7/CE1), U1.11 (AI1)
EN_UP_2: J3.29 (GPIO5), J4.29 (GPIO5), U1.10 (AI2)
GND: J3.6 (GND), J3.9 (GND), J3.14 (GND), J3.20 (GND), J3.25 (GND), J3.30 (GND), J3.34 (GND), J3.39 (GND), J4.6 (GND), J4.9 (GND), J4.14 (GND), J4.20 (GND), J4.25 (GND), J4.30 (GND), J4.34 (GND), J4.39 (GND), R3.2, U1.3 (GND), U1.8 (GND), U1.16 (GND), U2.3 (GND), U2.8 (GND), U2.13 (BI1), U2.14 (BI2), U2.16 (GND); also elsewhere on the board
GPIO2: J3.3 (GPIO2/SDA), J4.3 (GPIO2/SDA)
GPIO3: J3.5 (GPIO3/SCL), J4.5 (GPIO3/SCL)
GPIO12: J3.32 (GPIO12/PWM0), J4.32 (GPIO12/PWM0)
GPIO19: J3.35 (GPIO19/PWM1), J4.35 (GPIO19/PWM1)
ID_SC_UNUSED: J3.28 (ID_SC), J4.28 (ID_SC)
ID_SD_UNUSED: J3.27 (ID_SD), J4.27 (ID_SD)
LEVEL_EC_3V3: J3.16 (GPIO23), J4.16 (GPIO23); also elsewhere on the board
LEVEL_PH_DOWN_3V3: J3.18 (GPIO24), J4.18 (GPIO24); also elsewhere on the board
LEVEL_PH_UP_3V3: J3.22 (GPIO25), J4.22 (GPIO25); also elsewhere on the board
LEVEL_TRAY_BOTTOM_3V3: J3.19 (GPIO10/MOSI), J4.19 (GPIO10/MOSI); also elsewhere on the board
LEVEL_TRAY_TOP_3V3: J3.21 (GPIO9/MISO), J4.21 (GPIO9/MISO); also elsewhere on the board
LEVEL_WATER_3V3: J3.15 (GPIO22), J4.15 (GPIO22); also elsewhere on the board
MUX_EN: J3.31 (GPIO6), J4.31 (GPIO6); also elsewhere on the board
MUX_SEL0: J3.36 (GPIO16), J4.36 (GPIO16); also elsewhere on the board
MUX_SEL1: J3.38 (GPIO20), J4.38 (GPIO20); also elsewhere on the board
MUX_SEL2: J3.37 (GPIO26), J4.37 (GPIO26); also elsewhere on the board
MUX_SEL3: J3.40 (GPIO21), J4.40 (GPIO21); also elsewhere on the board
unnamed: D3.1 (K), R3.1
PWM0: J3.12 (GPIO18/PWM0), J4.12 (GPIO18/PWM0), U2.9 (PWMA), U2.15 (PWMB)
PWM1: J3.33 (GPIO13/PWM1), J4.33 (GPIO13/PWM1), U1.9 (PWMA), U1.15 (PWMB)
USER_LED_BUZZER: J3.13 (GPIO27), J4.13 (GPIO27); also elsewhere on the board
WATER_TEMP: J3.7 (GPIO4), J4.7 (GPIO4); also elsewhere on the board

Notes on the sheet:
pH Down
pH Up
Note: Motors connect via Deans Connectors
Note: Always On
POWER SUPPLY AND INDICATORS
MOUNTING HARDWARE
REMOTE CONTROL OUTLETS
Note: Bolded labels are locked pin assignments
GREEN
MOTORS, MOTOR DRIVER
RASPBERRY PI GPIO
ENVIRONMENTAL SENSORS
INTERFACE PCB
Nutrients

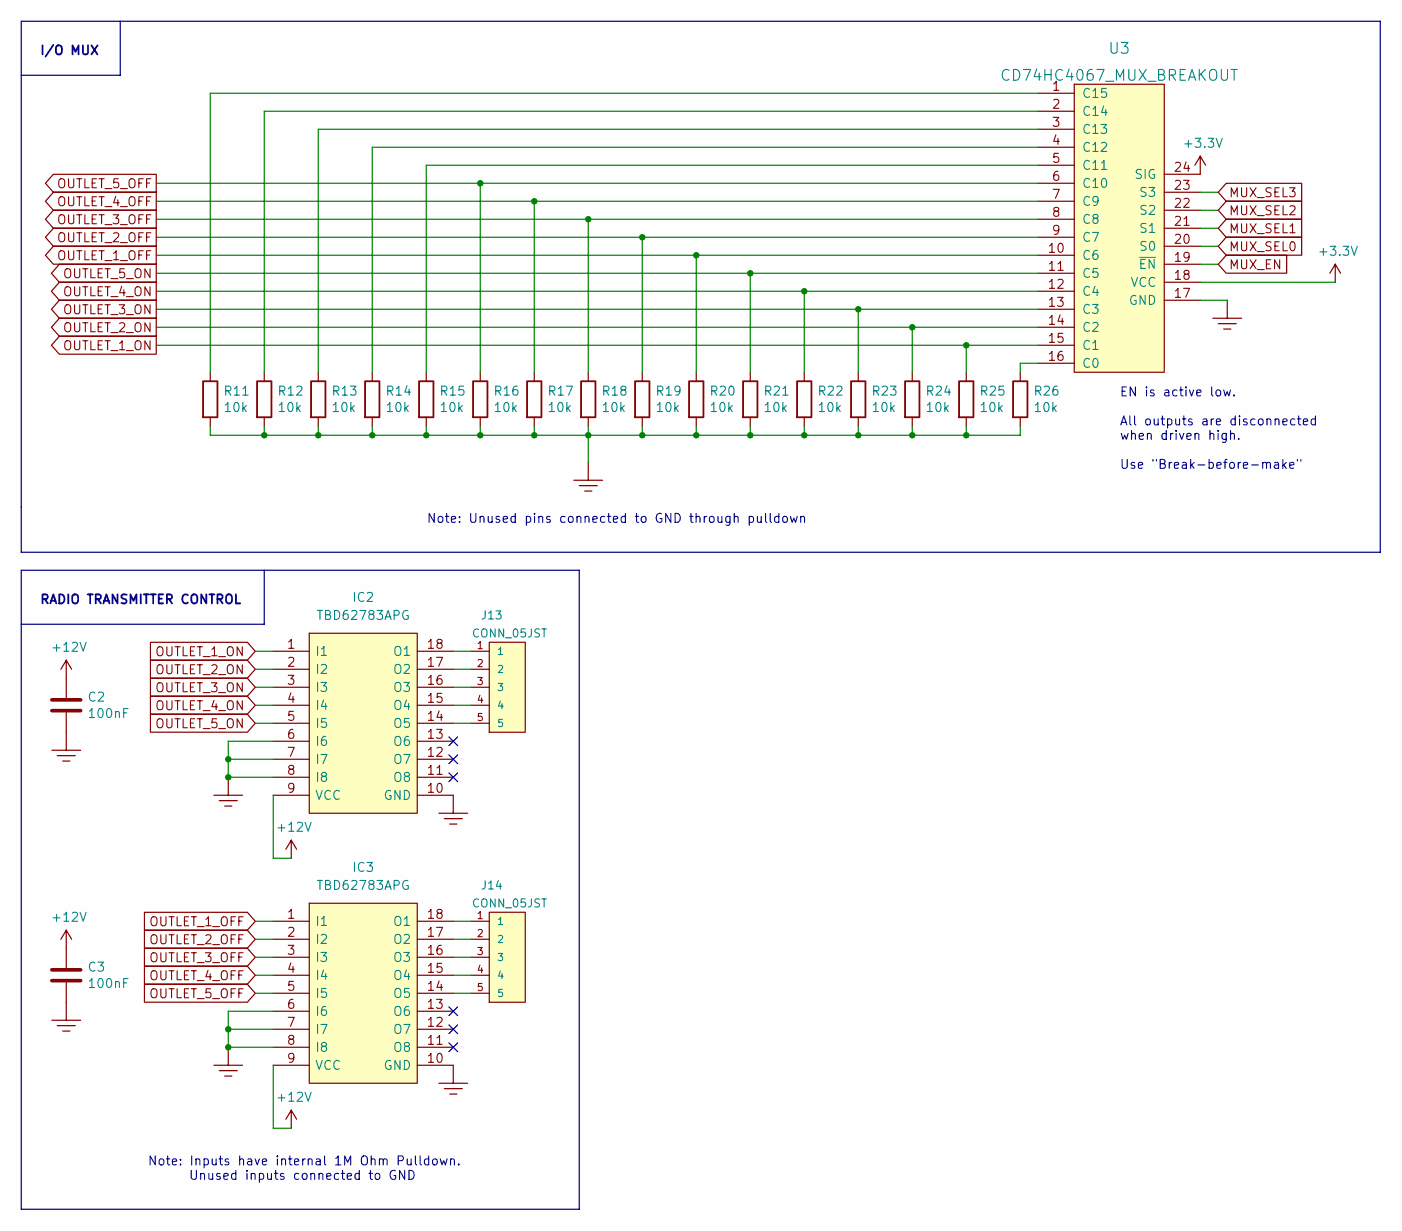
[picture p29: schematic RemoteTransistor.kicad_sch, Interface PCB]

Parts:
C2, C3: 100nF; C_Ceramic_Disc_D4.3mm_W1.9mm_P5.08mm
IC2, IC3: TBD62783APG; DIP-18_W7.62mm_Socket_IC; Digikey_Part_Number TBD62783APG-ND
J13, J14: CONN_05JST; JST_XH_1x05_P2.54mm_Vertical
R11, R12, R13, R14, R15, R16, R17, R18, R19, R20, R21, R22, R23, R24, R25, R26: 10k; R_SS_Axial_DIN0207_L6.3mm_D2.5mm_P10.16mm_Horizontal
U3: CD74HC4067_MUX_BREAKOUT; Digikey_Part_Number 1568-1181-ND

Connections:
+3V3: U3.18 (VCC), U3.24 (SIG); also elsewhere on the board
+12V: C2.1, C3.1, IC2.9 (VCC), IC3.9 (VCC); also elsewhere on the board
GND: C2.2, C3.2, IC2.6 (I6), IC2.7 (I7), IC2.8 (I8), IC2.10 (GND), IC3.6 (I6), IC3.7 (I7), IC3.8 (I8), IC3.10 (GND), R11.2, R12.2, R13.2, R14.2, R15.2, R16.2, R17.2, R18.2, R19.2, R20.2, R21.2, R22.2, R23.2, R24.2, R25.2, R26.2, U3.17 (GND); also elsewhere on the board
MUX_EN: U3.19 (~EN); also elsewhere on the board
MUX_SEL0: U3.20 (S0); also elsewhere on the board
MUX_SEL1: U3.21 (S1); also elsewhere on the board
MUX_SEL2: U3.22 (S2); also elsewhere on the board
MUX_SEL3: U3.23 (S3); also elsewhere on the board
unnamed: IC2.14 (O5), J13.5
unnamed: IC2.15 (O4), J13.4
unnamed: IC2.16 (O3), J13.3
unnamed: IC2.17 (O2), J13.2
unnamed: IC2.18 (O1), J13.1
unnamed: IC3.14 (O5), J14.5
unnamed: IC3.15 (O4), J14.4
unnamed: IC3.16 (O3), J14.3
unnamed: IC3.17 (O2), J14.2
unnamed: IC3.18 (O1), J14.1
unnamed: R11.1, U3.1 (C15)
unnamed: R12.1, U3.2 (C14)
unnamed: R13.1, U3.3 (C13)
unnamed: R14.1, U3.4 (C12)
unnamed: R15.1, U3.5 (C11)
unnamed: R26.1, U3.16 (C0)
OUTLET_1_OFF: IC3.1 (I1), R20.1, U3.10 (C6)
OUTLET_1_ON: IC2.1 (I1), R25.1, U3.15 (C1)
OUTLET_2_OFF: IC3.2 (I2), R19.1, U3.9 (C7)
OUTLET_2_ON: IC2.2 (I2), R24.1, U3.14 (C2)
OUTLET_3_OFF: IC3.3 (I3), R18.1, U3.8 (C8)
OUTLET_3_ON: IC2.3 (I3), R23.1, U3.13 (C3)
OUTLET_4_OFF: IC3.4 (I4), R17.1, U3.7 (C9)
OUTLET_4_ON: IC2.4 (I4), R22.1, U3.12 (C4)
OUTLET_5_OFF: IC3.5 (I5), R16.1, U3.6 (C10)
OUTLET_5_ON: IC2.5 (I5), R21.1, U3.11 (C5)

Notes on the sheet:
I/O MUX
Note: Unused pins connected to GND through pulldown
Note: Inputs have internal 1M Ohm Pulldown. Unused inputs connected to GND
RADIO TRANSMITTER CONTROL
EN is active low. All outputs are disconnected when driven high. Use "Break-before-make"

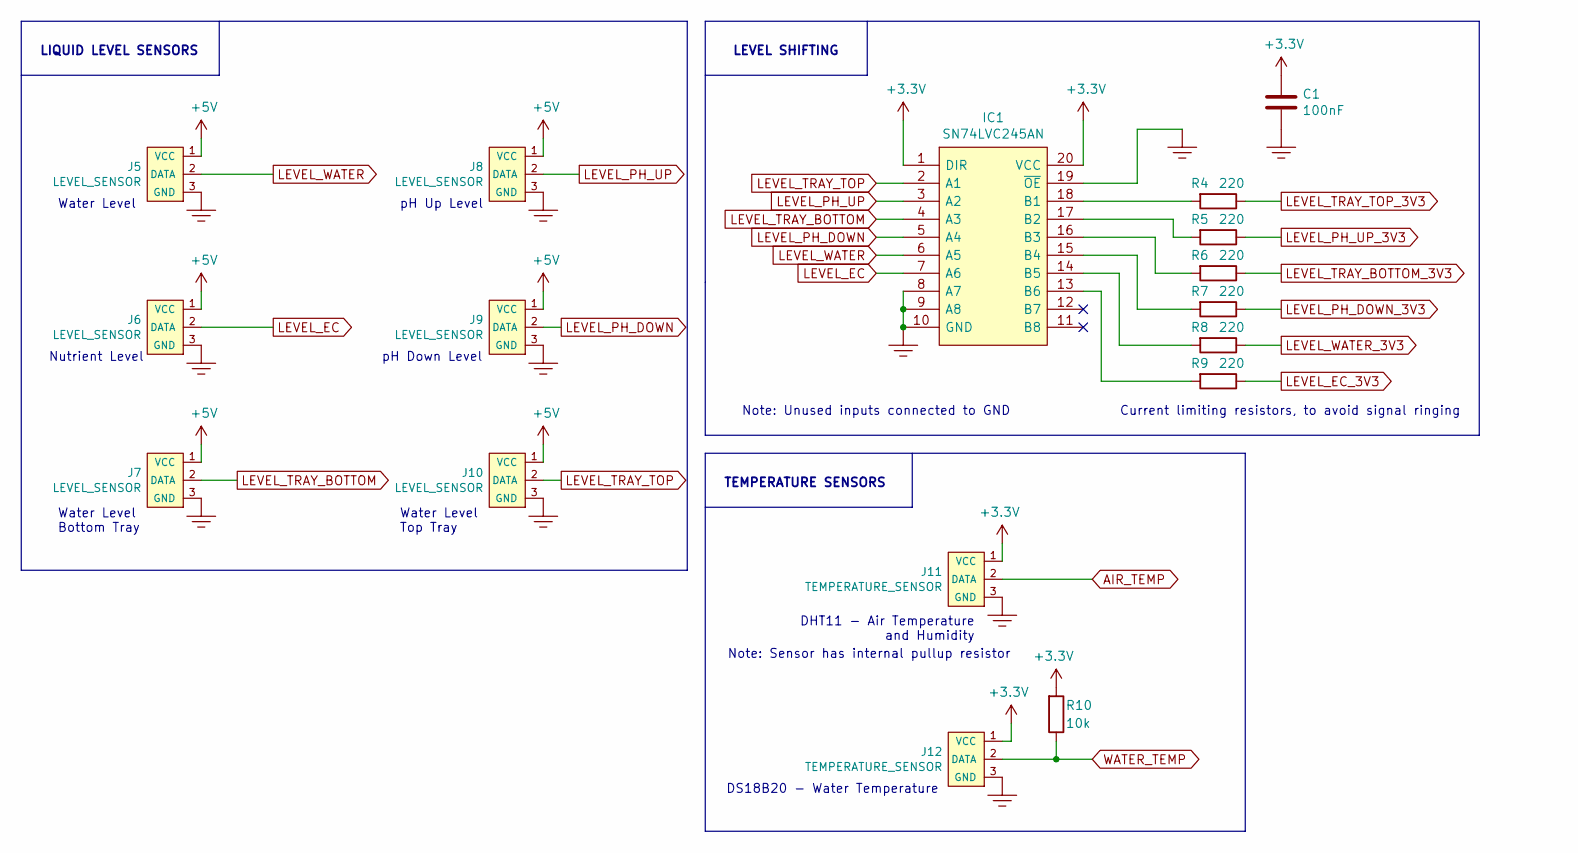
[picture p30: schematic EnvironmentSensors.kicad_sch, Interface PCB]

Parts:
C1: 100nF; C_Ceramic_Disc_D4.3mm_W1.9mm_P5.08mm
IC1: SN74LVC245AN; DIP-20_W7.62mm_Socket_IC; Digikey_Part_Number 296-8503-5-ND
J5, J6, J7, J8, J9, J10: LEVEL_SENSOR; JST_XH_1x03_P2.54mm_Vertical
J11, J12: TEMPERATURE_SENSOR; JST_XH_1x03_P2.54mm_Vertical
R4, R5, R6, R7, R8, R9: 220; R_SS_Axial_DIN0207_L6.3mm_D2.5mm_P10.16mm_Horizontal
R10: 10k; R_SS_Axial_DIN0207_L6.3mm_D2.5mm_P10.16mm_Horizontal

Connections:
+3V3: C1.1, IC1.1 (DIR), IC1.20 (VCC), J11.1 (VCC), J12.1 (VCC), R10.2; also elsewhere on the board
+5V: J5.1 (VCC), J6.1 (VCC), J7.1 (VCC), J8.1 (VCC), J9.1 (VCC), J10.1 (VCC); also elsewhere on the board
AIR_TEMP: J11.2 (DATA); also elsewhere on the board
GND: C1.2, IC1.8 (A7), IC1.9 (A8), IC1.10 (GND), IC1.19 (~OE), J5.3 (GND), J6.3 (GND), J7.3 (GND), J8.3 (GND), J9.3 (GND), J10.3 (GND), J11.3 (GND), J12.3 (GND); also elsewhere on the board
LEVEL_EC: IC1.7 (A6), J6.2 (DATA)
LEVEL_EC_3V3: R9.1; also elsewhere on the board
LEVEL_PH_DOWN: IC1.5 (A4), J9.2 (DATA)
LEVEL_PH_DOWN_3V3: R7.1; also elsewhere on the board
LEVEL_PH_UP: IC1.3 (A2), J8.2 (DATA)
LEVEL_PH_UP_3V3: R5.1; also elsewhere on the board
LEVEL_TRAY_BOTTOM: IC1.4 (A3), J7.2 (DATA)
LEVEL_TRAY_BOTTOM_3V3: R6.1; also elsewhere on the board
LEVEL_TRAY_TOP: IC1.2 (A1), J10.2 (DATA)
LEVEL_TRAY_TOP_3V3: R4.1; also elsewhere on the board
LEVEL_WATER: IC1.6 (A5), J5.2 (DATA)
LEVEL_WATER_3V3: R8.1; also elsewhere on the board
unnamed: IC1.13 (B6), R9.2
unnamed: IC1.14 (B5), R8.2
unnamed: IC1.15 (B4), R7.2
unnamed: IC1.16 (B3), R6.2
unnamed: IC1.17 (B2), R5.2
unnamed: IC1.18 (B1), R4.2
WATER_TEMP: J12.2 (DATA), R10.1; also elsewhere on the board

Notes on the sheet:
Water Level Top Tray
pH Down Level
DHT11 - Air Temperature and Humidity
Nutrient Level
LIQUID LEVEL SENSORS
Water Level
LEVEL SHIFTING
Note: Unused inputs connected to GND
TEMPERATURE SENSORS
Water Level Bottom Tray
pH Up Level
DS18B20 - Water Temperature
Note: Sensor has internal pullup resistor
Current limiting resistors, to avoid signal ringing

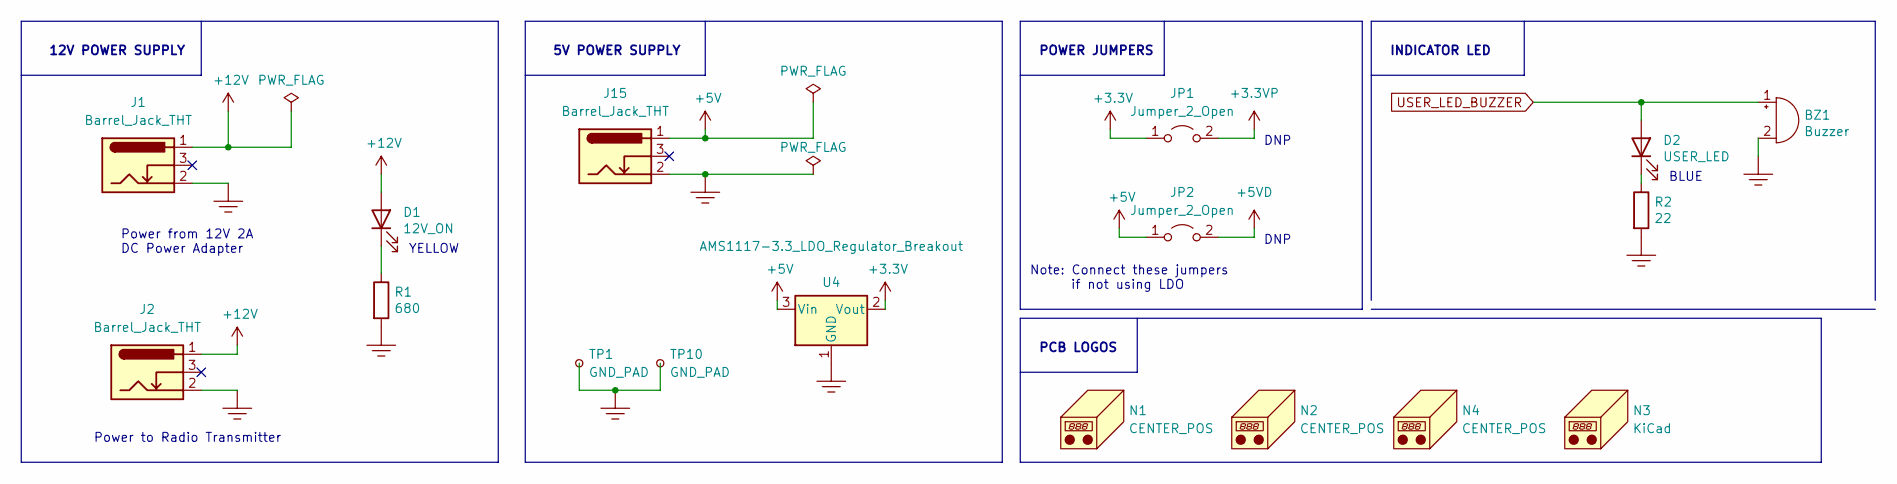
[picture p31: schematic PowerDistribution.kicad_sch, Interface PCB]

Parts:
BZ1: Buzzer; Buzzer_Generic_D12.2mm_H6.5mm
D1: 12V_ON; LED_SS_1206_3216Metric_Pad1.42x1.75mm_HandSolder
D2: USER_LED; LED_SS_1206_3216Metric_Pad1.42x1.75mm_HandSolder
J1, J2, J15: Barrel_Jack_THT; BarrelJack_Horizontal
JP1, JP2: Jumper_2_Open; R_SS_Axial_DIN0207_L6.3mm_D2.5mm_P10.16mm_Horizontal
N1, N2, N4: CENTER_POS; Polarity_Center_Positive_7.5mm_SilkScreen
N3: KiCad; KiCad-Logo2_8mm_SilkScreen
R1: 680; R_SS_Axial_DIN0207_L6.3mm_D2.5mm_P10.16mm_Horizontal
R2: 22; R_SS_Axial_DIN0207_L6.3mm_D2.5mm_P10.16mm_Horizontal
TP1, TP10: GND_PAD; TestPoint_Pad_5.0x5.0mm
U4: AMS1117-3.3_LDO_Regulator_Breakout; AMS1117-3.3_LDO_Regulator_Breakout_Board

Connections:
+3.3VP: JP1.2 (B); also elsewhere on the board
+3V3: JP1.1 (A), U4.2 (Vout); also elsewhere on the board
+5V: J15.1, JP2.1 (A), U4.3 (Vin); also elsewhere on the board
+5VD: JP2.2 (B); also elsewhere on the board
+12V: D1.2 (A), J1.1, J2.1; also elsewhere on the board
GND: BZ1.2 (+), J1.2, J2.2, J15.2, R1.2, R2.2, TP1.1, TP10.1, U4.1 (GND); also elsewhere on the board
unnamed: D1.1 (K), R1.1
unnamed: D2.1 (K), R2.1
USER_LED_BUZZER: BZ1.1 (-), D2.2 (A); also elsewhere on the board

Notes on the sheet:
POWER JUMPERS
Power from 12V 2A DC Power Adapter
YELLOW
DNP
INDICATOR LED
12V POWER SUPPLY
Note: Connect these jumpers if not using LDO
BLUE
5V POWER SUPPLY
PCB LOGOS
Power to Radio Transmitter

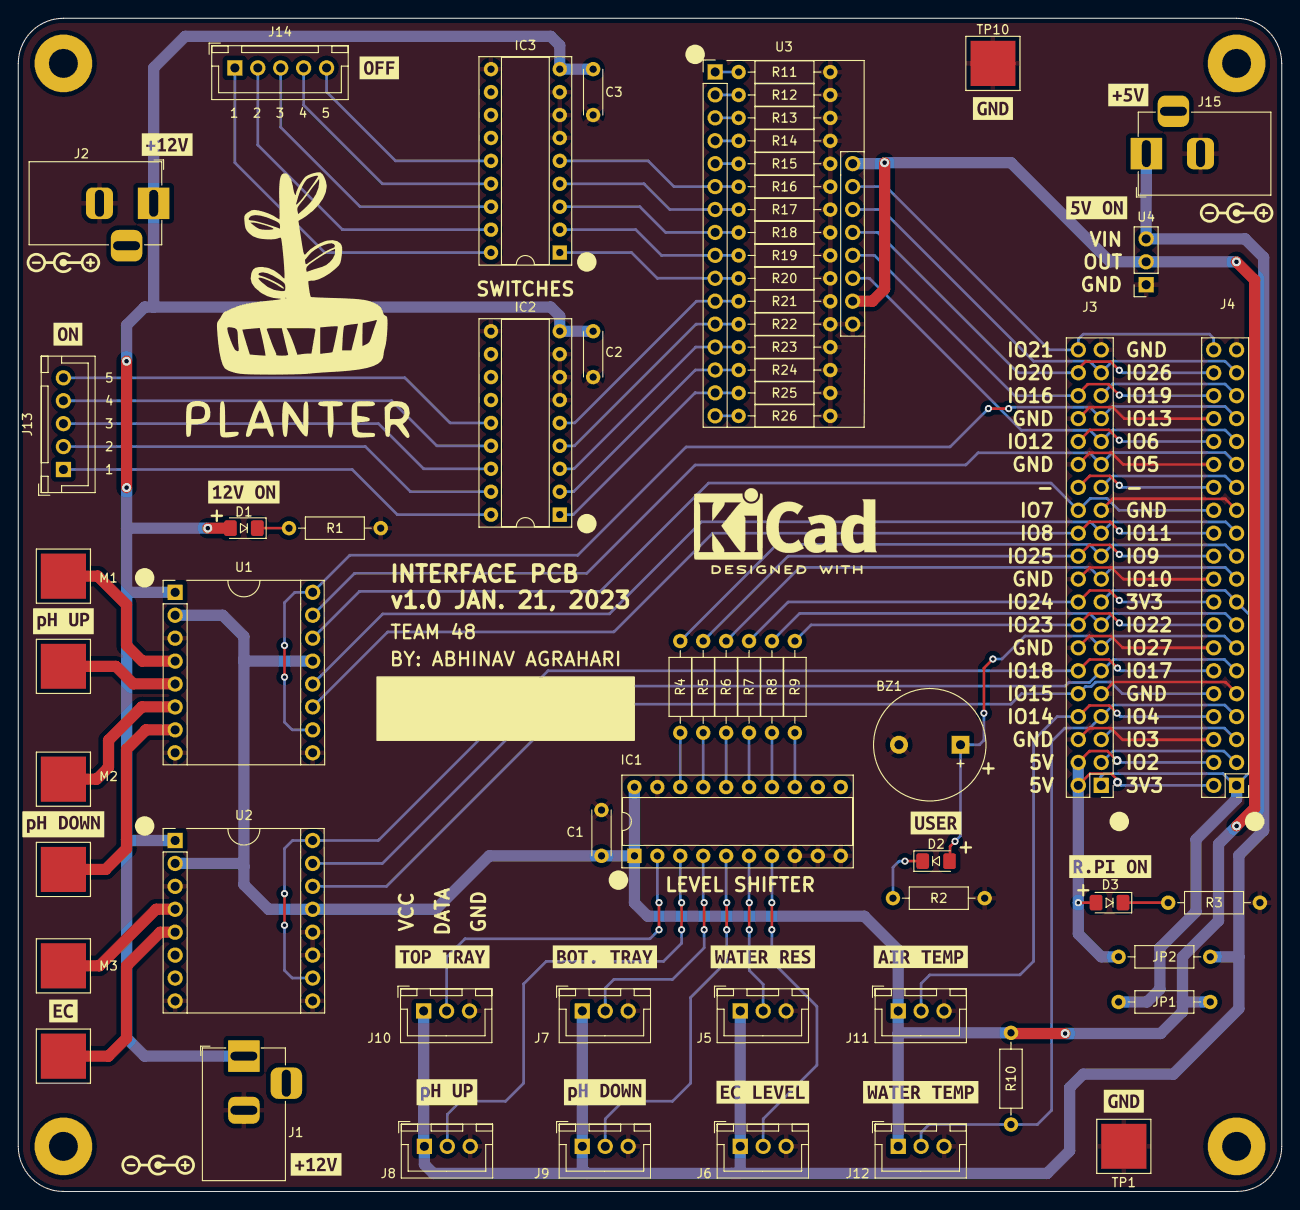
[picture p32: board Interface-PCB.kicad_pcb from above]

Board: 2 copper layers, 140.0 x 130.0 mm, 93 parts (0 on the bottom side), 81 nets.

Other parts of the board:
kibuzzard-63CB80E4: G***; kibuzzard-63CB80E4
kibuzzard-63CB87CD: G***; kibuzzard-63CB87CD
kibuzzard-63CB87D2: G***; kibuzzard-63CB87D2
kibuzzard-63CB811C: G***; kibuzzard-63CB811C
kibuzzard-63CB813E: G***; kibuzzard-63CB813E
kibuzzard-63CB856E: G***; kibuzzard-63CB856E
kibuzzard-63CB864A: G***; kibuzzard-63CB864A
kibuzzard-63CB8107, kibuzzard-63CB8107#2: G***; kibuzzard-63CB8107
kibuzzard-63CB8123: G***; kibuzzard-63CB8123
kibuzzard-63CB8136: G***; kibuzzard-63CB8136
kibuzzard-63CB8267: G***; kibuzzard-63CB8267
kibuzzard-63CB8415: G***; kibuzzard-63CB8415
kibuzzard-63CB8663, kibuzzard-63CB8663#2: G***; kibuzzard-63CB8663
kibuzzard-63CB8737, kibuzzard-63CB8737#2: G***; kibuzzard-63CB8737
kibuzzard-63CBAC35: G***; kibuzzard-63CBAC35
kibuzzard-63CC71CC: G***; kibuzzard-63CC71CC
kibuzzard-63CC577E: G***; kibuzzard-63CC577E
kibuzzard-63CDEE5A: G***; kibuzzard-63CDEE5A
kibuzzard-63CDEE7D: G***; kibuzzard-63CDEE7D

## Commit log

2022-11-15 First draft
    [Interface-PCB.kicad_pcb, Interface-PCB.sch]
2022-11-15 Split schematic sheets
    [EnvironmentSensors.sch, IOMux.sch, Interface-PCB.kicad_pcb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]
2022-11-16 Initial layout for FDP
    [Interface-PCB.kicad_pcb]
2022-11-20 Assign misc footprints for FDP
    [EnvironmentSensors.sch, Interface-PCB.kicad_pcb, Interface-PCB.sch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]
2022-12-04 Change to Highside switch
    [Interface-PCB.kicad_pcb, RemoteTransistor.sch]
2023-01-08 Add diagrams and datasheets
    [EnvironmentSensors.sch, Interface-PCB.sch, RemoteTransistor.sch]
2023-01-08 Review Schematic
    [EnvironmentSensors.sch, Interface-PCB.kicad_pcb, Interface-PCB.sch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]
2023-01-08 Add indicator LEDs
    [EnvironmentSensors.sch, Interface-PCB.sch, RemoteTransistor.sch]
2023-01-08 Reorder Remote Transistors
    [Interface-PCB.sch, LED_resistors.xlsx, RemoteTransistor.sch]
2023-01-08 Upgrade project to KiCad 6
    [EnvironmentSensors.kicad_sch, EnvironmentSensors.sch, IOMux.sch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]
2023-01-10 Update schematic based on breadboard tests
    - Add current limiting resistors to Level Shifter output
    - Add pull down resistors on all Mux outputs
    [EnvironmentSensors.kicad_sch, Interface-PCB.kicad_pcb, Interface-PCB.kicad_sch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]
2023-01-19 Setup JLCPCB Plotting Rules
    [Interface-PCB.kicad_pcb]
2023-01-19 Add test points and pads
    [EnvironmentSensors.kicad_sch, Interface-PCB.kicad_sch, LED_resistors.xlsx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]
2023-01-19 Add Planter Logo to schematic
    [Interface-PCB.kicad_sch]
2023-01-20 Add footprints for pads
    [EnvironmentSensors.kicad_sch, Interface-PCB.kicad_sch, RemoteTransistor.kicad_sch]
2023-01-20 Add breakout board and IC footprints
    - MUX
    - Motor Driver
    - PDIP ICs
    - LEDs
    [EnvironmentSensors.kicad_sch, Interface-PCB.kicad_sch, RemoteTransistor.kicad_sch]
2023-01-20 Add JST Connector Footprints
    [EnvironmentSensors.kicad_sch, Interface-PCB.kicad_sch, RemoteTransistor.kicad_sch]
2023-01-20 Update Header pin and Buzzer Footprints
    [EnvironmentSensors.kicad_sch, Interface-PCB.kicad_sch]
2023-01-20 Add JLC design rules
    [Interface-PCB.kicad_pcb]
2023-01-21 Complete Initial Layout of PCB
    - aligned to 5mm grid
    - 100x100mm board
    - update footprints
    - align 2 resistors to 2.54mm spacing
    [EnvironmentSensors.kicad_sch, Interface-PCB.kicad_pcb, Interface-PCB.kicad_sch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]
2023-01-21 Increase board size, Add connector labels
    - Increase board size to 140x130mm
    - Refine layout on PCB
    - Align breakout board resistors to 2.54mm spacing
    - Add Inverted silkscreen labels for off-board connectors
    [EnvironmentSensors.kicad_sch, Interface-PCB.kicad_pcb, Interface-PCB.kicad_sch]
2023-01-21 Create ground plane, swap motor driver pins
    - Create Ground pour/plane on F.Copper
    - Swap motor driver pin assignments, to resolve some route
    criss-crossing
    [Interface-PCB.kicad_pcb, Interface-PCB.kicad_sch]
2023-01-21 Align DIP-socket resistors with 2.54mm pin spacing
    [Interface-PCB.kicad_pcb, Interface-PCB.kicad_sch]
2023-01-21 Complete PCB layout
    - Complete component positioning and PCB layout
    - Swap most pin assignments to resolve track route criss-crossing
    [EnvironmentSensors.kicad_sch, Interface-PCB.kicad_pcb, Interface-PCB.kicad_sch]
2023-01-21 Update Blue LED resistor value
    [EnvironmentSensors.kicad_sch, Interface-PCB.kicad_pcb, Interface-PCB.kicad_sch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]
2023-01-21 Update symbols from library
    [EnvironmentSensors.kicad_sch, Interface-PCB.kicad_pcb, Interface-PCB.kicad_sch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]
2023-01-22 Add silkscreen and logos to PCB
    Complete silkscreen layer on PCB
    [EnvironmentSensors.kicad_sch, Interface-PCB.kicad_pcb, Interface-PCB.kicad_sch]
2023-01-22 Swap more pin assignments
    [EnvironmentSensors.kicad_sch, Interface-PCB.kicad_pcb, Interface-PCB.kicad_sch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]
2023-01-22 Complete PCB routing
    - Complete routing of all tracks
    - DRC shows no errors, only non-warnings for kicad-buzzard related items
    - Remove Level Sensor test points
    [EnvironmentSensors.kicad_sch, Interface-PCB.kicad_pcb, Interface-PCB.kicad_sch]
2023-01-22 Add Gerber and PDF exports
    [Interface-PCB-B_Cu.gbl, Interface-PCB-B_Mask.gbs, Interface-PCB-B_Paste.gbp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]
2023-01-23 Add 3.3V LDO Regulator and Barrel Jack Connectors
    - Add mounted barrel jack connectors for 12V and 5V
    - Add 5V to 3.3V LDO breakout board
    - Adjust silkscreen
    - Export and verify Gerbers
    [EnvironmentSensors.kicad_sch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]
2023-01-23 Move Remote Control Barrel Jack
    - Move a barrel jack
    - Export Gerbers again
    - Update images
    [Interface-PCB-B_Cu.gbl, Interface-PCB-B_Mask.gbs, Interface-PCB-B_Paste.gbp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]
2023-01-25 Add PDF outputs of PCB and SVG output of schematic
2023-02-21 Start Rev 1.1, Add pulldowns on Mux Input
    [EnvironmentSensors.kicad_sch, Interface-PCB.kicad_sch, PowerDistribution.kicad_sch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]
2023-02-22 Update README with images of manufactured PCB
